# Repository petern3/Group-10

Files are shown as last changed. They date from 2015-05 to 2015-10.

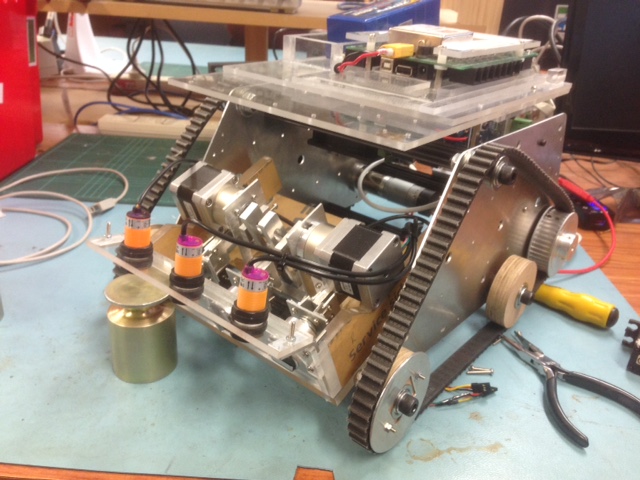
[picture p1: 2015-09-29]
Reports/Photos/IMG_0562.JPG

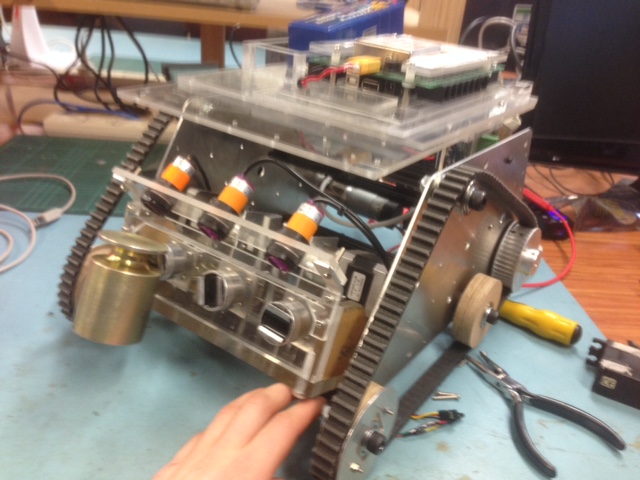
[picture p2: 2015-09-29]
Reports/Photos/IMG_0563.JPG

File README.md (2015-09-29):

# Group-10
Code and reports for the 2015 contest

Authors: Jack, Peter, Ryan

This is a full year assignment which includes:
- Automating a robot to move around a course and retrieve weights
- Writing three progress reports

Useful links
http://www.societyofrobots.com/sensors_sharpirrange.shtml

*Todo*
Mechanical:
- [ ] Track support bring dampers
- [ ] Tilt Mechanism wire test
- [ ] Front brace
- [ ] Reliable weight removal (may come with tilt) stepper driver
- [ ] General tidying up

Electrical:
- [ ] Circuits - ordering parts, PCB
- [ ] Mount IMU etc
- [ ] Limit switches
- [ ] Mount custom circuits
- [ ] Mount other sensors
- [ ] Tidy cables

Software:
- [ ] Redo secondary tactic - wall avoiding, weight detecting, etc with as few 'if' statements as possible
- [ ] Extensive testing and calibrate
- [ ] State estimate
- [ ] State correct
- [ ] Place landmarks (first place that needs map)
- [ ] D*
- [ ] Audio to play off SD

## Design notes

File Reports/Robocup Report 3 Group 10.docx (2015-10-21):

University of Canterbury

# Robocup Progress Report 3

Group 10

Jack Hendrikz
Peter Nicholls
Ryan Taylor

20 October 2015

# 0.0 Executive Summary

This evaluation report (ER) assesses the performance of Group 10s robot in the second annual package-collection Robocup competition. This competition is a challenge where an autonomous robot has 5 minutes to navigate and retrieve as many packages as possible within an unknown arena layout. Group 10 came fourth in a series of knock out rounds. The group competed in a total of four rounds, two of which were won, the other two of which were lost. During these rounds, the robot collected a total 5.25kg worth of food packages, equivalent to just over 1.3kg per round.

The method of package collection was to use three permanent magnets, and used a form of slider-crank to remove the packages from the magnets. Four infrared sensors and three ultrasonic sensors were used to navigate and search the arena. Once a package was seen, it took 0.5 seconds to collect it. The unique track layout could provide a top speed of approximately 0.65ms^(-1) . When a package was collected, an array of digital IR sensors positioned above the magnets confirmed the collection.

This report evaluates the robot against the initial design requirements discussed in the conceptual and detailed design reports (CDR and DDR), followed by a comparison with the four robots challenged. The aspects of the robot that performed well were the permanent magnet collection method and the ground clearance. The two main ways the robot failed was that it could not drop off packages reliably, and the watchdog timer had not been tested in all cases.

The performance of other robots during the competition was variable, with both successes and failures. Group 3 had a robust mechanical magnetic pickup mechanism along with a simple storage and drop off system. Group 12 used speed to their advantage, along with a passive pickup mechanism. Group 6 in contrast had a terrible locomotion system, causing it to become lodged on uneven terrain at several points during the competition.

For the robot to have progressed further in the competition, a better watchdog timer and more reliable package detection should be implemented. This timer, used in tandem with the IMU’s accelerometer, would trigger if the robot had not accelerated for 10 seconds. This would only occur when the robot became stuck against arena obstacles. Package detection had a maximum range of 300mm and could be improved with the use of cameras and infrared diodes.

# 1.0 Introduction

This the final report and assessment for the 2015 Robocup. The Robocup competition is a challenge where an autonomous robot must be designed to search and retrieve packages in an arena. The arena has a series of obstacles unknown to the team, and included walls, poles and uneven ground. The packages are placed in specific but unknown points within the arena, with varying collection difficulty. The packages were also of unknown mass, more mass being worth more points. Two robots competed to get the most mass from the packages.

Each round lasted 5 minutes, and if the winner could not be determined by the total mass collected, then the robot furthest from base would be declared the winner. The competition was structured as a double-elimination tournament such that the winner of each round would continue to the next round, and also allowed for one loss in the competition. The limit of three packages on board meant returning to base was essential to getting more than three packages.

For this to be accomplished, there are many crucial sub-systems that are required to work in unison. These can be split into two main categories:

- Locomotion - how the robot will move, avoid walls and return to base
- Package Manipulation - how the robot will detect, collect and release packages

Both of these require detailed software, electronic interfaces, sensors and mechanical interfaces with the environment. There are also several non-critical subsystems which will also be discussed in lesser details. Such subsystems include the three constructed PCBs.

This report will analyse several aspects of the finished robot, starting with a how it compares with our previous designs in the CDR and DDR, and secondly it's performance in the arena. The performance of our robot against that of four other competitors will also be analysed. Final suggestions for the future evolution of the robot will be put forward as if it was to compete again.

# 2.0 Design Description

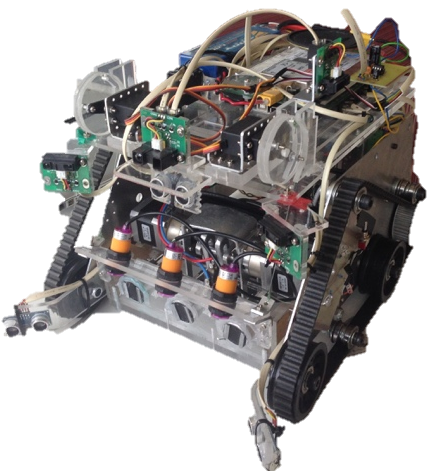
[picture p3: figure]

Figure 1: The final design used in the competition

The final robot design is shown in Figure 1. Three permanent magnets were used to collect and store packages, which could then be raised and lowered using two servos. One ultrasonic and four infrared (IR) sensors were used for navigation, two ultrasonic sensors were used for package detection, and three digital IR sensors were used to detect when a package was on board. 3D printed wheels provided the robot with good ground clearance and greater mobility.

The software we used had effective wall and object avoidance, but had inefficient package detection. Because the ultrasonic sensors used for package detection were noisy, a compromise between response time and accuracy had to be made. Unfortunately we were not able to reliably detect packages which lead to time being wasted by driving past them. Figure 2 shows the overall flow of software used in the competition. The software set a target in Cartesian coordinates to drive towards, which took into account the walls, packages and bases. Using Cartesian coordinates made it easier when linking the sensor information input to driving output.

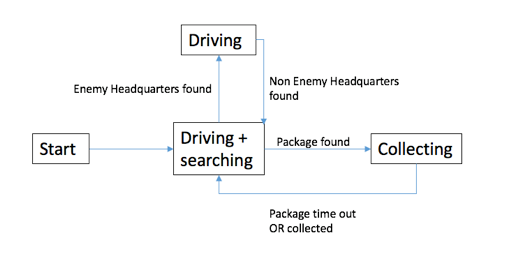
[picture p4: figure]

Figure 2: The final flow of software

## 2.1 Locomotion

### 2.11 Mechanical Layout

The bumps were 17mm high and 3D printed wheels were used to raise the minimum height of the robot to 25mm . Having a shortened wheel base improved the turning speed and mobility of the robot. Although this model did not give a speed advantage, the robot was fast enough that the drive wheels did not require modification. Figure 3 shows the robot track design with the centre of gravity. The track layout was left as described in the CDR and DDR.

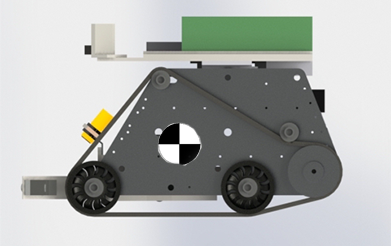
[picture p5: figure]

Figure 3: Track configuration and centre of gravity of the robot

### 2.12 Sensor Layout

One ultrasonic and four IR sensors were used to navigate the arena and avoid obstacles. Two medium IR sensors were mounted on the front of the robot and set at an angle of 27 degrees from the centre-line of the robot. This ensured that they would intersect with the ultrasonic sensor beams which enabled them to be compared. This comparison helped the robot distinguish between obstacles and packages.

The long range IR sensor was mounted in the middle front of the robot and helped with terrain navigation. It was predominantly used to detect corners and allow the robot to move through gaps. It could also be used for pole detection if the robot was approaching the pole.

The centrally mounted ultrasonic sensor was added to compliment the long range IR as it is more effective at detecting poles. This helped ensure that the robot would not become stuck on the poles around the arena. An extra short range IR was mounted on the top of the robot facing left. This aided wall avoidance and helped determine whether it was approaching a corner or not.

### 2.13 Software Algorithms

The software had a series of cases for different sensor readings, each of which would place the target in a different position. This was done approximately every 300ms . Each case compared the sensor values to determine the layout of its surrounding environment, and made suitable navigational decisions. This made it easy to debug each case the robot encountered. There were a total of 16 different cases.

A watchdog timer was also coded to prevent the robot from becoming stuck on obstacles around the arena. To implement a watchdog timer, the location of the target was monitored. If the target had not moved for six seconds, then the robot reversed and then rotated. This method worked well when the robot was stuck in a corner, bump or pole, but caused issues in the presence of another robot, and is discussed later.

This algorithm implemented the secondary tactic, as opposed to the primary tactic due to time constraints. This tactic was described in the DDR but would only be utilised if the primary tactic failed.

## 2.2 Package Manipulation

### 2.21 Pickup Mechanism

The pickup mechanism used three permanent magnets to retain the packages. When a package was detected the robot would lower the magnets ready for collection and once the package was on board it would subsequently raise the magnets. A system was in place to retract the magnets, allowing them to be detached when the mechanism was retracted. In doing so, the magnetic force would be smaller than gravitational force on the packages, thus dropping the packages. Two geared stepper motors (FIT0349) were used to operate the system which converted rotational motion to linear motion. Figure 4 shows the pickup mechanism design with the magnets on the front and digital IR on the front. Figure 5 shows a section view of the mechanism. As the geared stepper rotates the eccentric shaft is spun around, which makes the link rotate back and forward. The magnets are connected through the rod to the link, providing linear motion. Feedback was achieved as to when the magnets were extended by a limit switch, and when a package was being stored by the digital IR sensors. The only changes to this system from the DDR was the addition of a limit switch and reinforcing brackets.

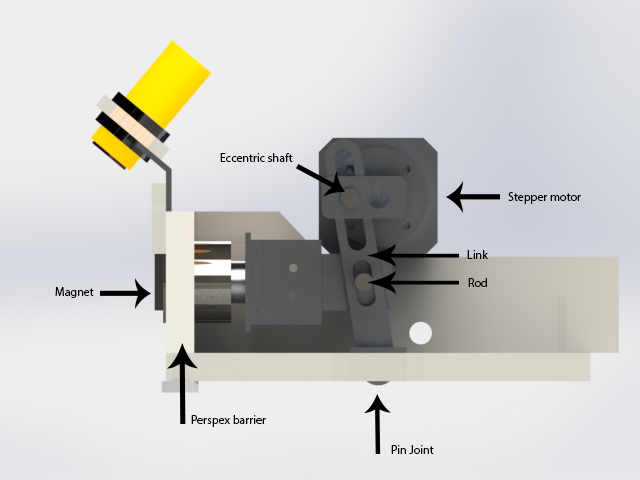
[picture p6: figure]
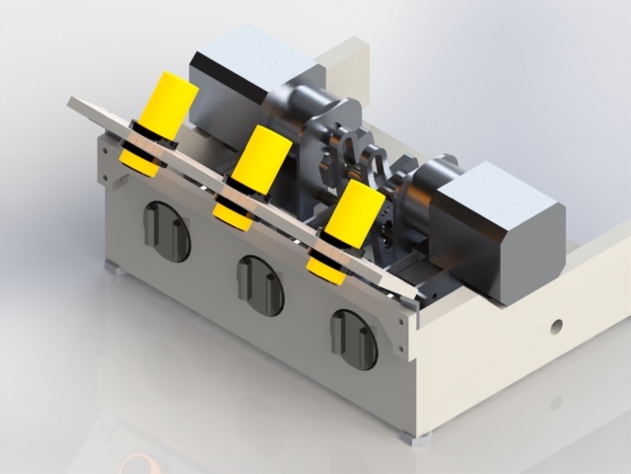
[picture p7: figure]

Figure 4: The overall pickup mechanism

Figure 5: Components within the pickup mechanism

### 2.22 Sensor Layout

Ultrasonic sensors were used to find packages, they were mounted 40mm above the floor in front of the robot. When choosing the angle, if the angle was larger, the robot had a reduced range but had a wider field-of-view. They were placed at an angle of 50 degrees so the viewing angle was a total of 130 degrees. While it could not see packages in the 70 degrees in front of it, these package would fall within view of the ultrasonic sensors at some point. This was as outlined in the DDR.

### 2.23 Software Algorithms

When one of the ultrasonic sensors registered a distance, it would read the IR and ultrasonic sensors on top of the robot and determine whether or not the point given was a wall, pole or package. If it was a package, then the distance was calculated from the difference between ultrasonic sensors and IR sensor, and then the relative Cartesian coordinate would be computed.

When a package was detected, the robot placed the target on top of the reading. To reduce the effect of 'false positives' given by the ultrasonic sensors, three checks were done. Firstly, the robot would only decide that a package was indeed a package after detecting it three consecutive times. Secondly, the amount of time spent chasing the package was directly proportional to the number of times detected. This allowed time to pick up the package once in the robot's inner blind spot. Thirdly, when aligning with a package, the robot would move slower. This was good as it has reduced probability of driving into walls, but it also made it much slower when nearing a package (as the speed was proportional to the distance from the target).

Because there were three digital IR sensors which could determine which magnets had collected packages, the robot could aligned such that the packages would collect on the empty magnets. When all three digital IR sensors were active, the robot would not attempt to collect packages. The robot would also not collect packages when it either base. This was how the DDR described the package detection.

## 2.3 Non-crucial Subsystems

### 2.31 Audio Amplifier

Since the Arduino is not able to supply much current, attaching a speaker straight to the pins could not provide the volume wanted. The amplifier board was so successful that while it was not receiving a signal, it would amplify the electrical noise generated by the fan. To prevent this, a transistor was used to enable or disable the speaker. This meant it would be enabled only when it needed to be used.

### 2.32 Switch bank

The bank of eight switches was a useful addition to the robot which ought to have been implemented earlier. Although it wasn't really used in the actual competition, it was very useful when testing. Each of the switches were bound to a different statement in code which enabled different behaviours such as whether or not to release packages and disabling the motors. Each of these were useful when testing.

### 2.33 Light Array

This was initially intended to contain a bank of IR LEDs as well as mount the IR camera, there was not sufficient time to implement the camera. As such, the IR LEDs were not required, so standard LEDs were used for nothing more than to confuse other robot's cameras.

# 3.0 Design Evaluation of Robot

## 3.1 General

#### R1.1 The robot will be fully autonomous ✔

#### R1.2 The robot will be controlled by the Arduino Mega ADK supplied ✔

#### R1.3 The robot shall be able to move, identify and collect packages ✔

#### R1.4 The robot shall operate until all 11 packages are claimed or the time limit is reached ✔

The robot was fully autonomous throughout the competition through the use of the supplied Arduino Mega ADK as specified in R1.1 and R1.2. The robot had the ability to move, identify, and collect packages within the arena with the use of ultrasonic sensors as per R1.3. During the tournament, the robot collected seven packages, weighing a total of 5.25kg . Although the robot collected this many packages, there were another approximately 20 packages that were either not detected (and should have been) or unable to be collected at all. This gave the robot a successful collection rate of 35%.

The robot fulfilled R1.4 as it operated for the full five minutes that the match lasted. There were not issues with the robot running out of power during operation, but the robot was immobilised during the third round. It could be noted that there was no counter implemented to instruct the robot to cease package detection after all 11 packages had been claimed.

## 3.2 Identification

#### R2.1 The robot shall be able to identify food packages ✔

#### R2.2 The robot shall be able to identify obstacles it cannot move over ✔

#### R2.3 The robot shall be able to distinguish home HQ and the opposition HQ ✔

#### R2.4 The robot should rely on a range of navigational sensors ✔

The robot could identify packages as per R2.1, however it did have reliability issues. It detected approximately 60% of the packages within the sensors’ range, but there were also several false positives detected. The arena walls had a curved skirting which on occasion would be read as a package. Poles were also another obstacle that would flag a false positive due to the offset of the ultrasonic and IR sensors. While they were placed to reduce false positives, there was a small region in front of the robot that is detected by the ultrasonic sensor but not the medium IR sensors, and was hence interpreted as a package. This meant that the robot moved towards what the false ‘package’. Once the robot was close enough, the sensors could not read accurately. This is when the watchdog timer kicked in and caused the robot to reverse and turn. The false positives could have been reduced through the additional use of an alternative package detection system.

The robot performed well when it came to identifying its surrounding environment. The use of four different types of navigational sensors satisfied R2.2 and R2.4. A total of five sensors were used for navigation along with two sensors for package detection. This sensor array meant the robot reduced collisions with the arena to approximately four per minute. The only problem encountered during the competition when navigating was that the robot often steered towards poles (as discussed previously), which raised this collision rate to over six per minute.

Once calibrated, the robot could accurately distinguish between home HQ and opposition HQ. This was achieved via the Adafruit TCS3472 colour sensor mounted on the underside of the robot. The robot never attempted to collect a package in either base, and so R2.3 was satisfied. Overall the robot's environment detection performed well at a basic level during the competition, but could have functioned more robustly with more comprehensive calibration and testing.

## 3.3 Movement

#### R3.1 The robot shall be able to move over obstacles at least 25mm in height ✔

#### R3.2 The robot shall be able to fit through gaps of at least 500mm in width ✔

#### R3.3 The robot shall be able to manoeuvre around obstacles it cannot move over ✔

#### R3.4 The robot shall not leave the designated arena during the competition ✔

#### R3.5 The robot should not get stuck in any algorithmic loops for longer than 1 minute ✘

The design of the locomotion allowed the robot to operate well within the arena during the competition. The 3D printed wheel and track design allowed the robot to drive over obstacles at a speed of about 0.65ms^(-1) as per the requirements of R3.1. The design was kept compact, allowing the robot to move through arena obstacle gaps of at least 500mm , specified in R3.2. Once obstacles too large to move over were detected, the robot could navigate efficiently around them, thus fulfilling R3.3. There was no physical way that the robot could leave the arena during operation, meeting requirement R3.4.

The robot did suffer from a few design issues, one of which was that the tracks detached occasionally, once during the competition. This only happened on uneven terrain, as the belts lost tension and subsequently slipped off the wheels. This could have been avoided through providing more belt tension and installing brackets to prevent the belt from slipping off the wheels.

During testing it was noticed that the front of the aluminium chassis would flex outwards by 5mm on both sides. This flexing was put down to the belt tension and lack of bracing on the front of the robot. Bracing was difficult to achieve as it would have obstructed the pickup mechanism. Side bracing could have solved this issue, but there was insufficient time to test this solution.

For R3.5, steps were taken to prevent the robot from getting stuck in algorithmic logic loops for longer than one minute, however, not all issues were remedied before the competition day. A watchdog timer was implemented to prevent the robot from becoming stuck on terrain in the arena. This worked when stuck against terrain, but had not been tested with another robot. As the opposition robot moved, the robot's target would change and therefore reset the timer. In addition to checking the change in target, the accelerometer could have assisted in detecting when the robot had stopped.

## 3.4 Collection

#### R4.1 The robot shall be able to pick up a package so that it is under the robot’s control ✔

#### R4.2 The robot shall have a way of carrying, at most, three packages without hindrance ✔

#### R4.3 The robot shall not collect any packages within the opposition’s HQ ✔

#### R4.4 The robot should be able to release any packages it has on-board to HQ ✘

#### R4.5 The robot should be able to pick up packages in any orientation and any part of the map ✘

The collection mechanism of the robot performed well in the arena, and was the sole reason that the robot succeeded on the day. The versatility of the permanent magnets allowed three packages to be picked up under the robot's control, thus fulfilling R4.1 and R4.2. Two HX12K servo motors were used to lift the pickup mechanism for two reasons: so that the packages did not catch on uneven ground, and to prevent collection of opposition packages within their HQ. This meant that the robot also met criteria R4.3 during the competition.

The robot was programmed and designed so that packages could be dropped off in its HQ when the corresponding colour was detected. The magnet strength was underestimated during the calculation phase of the robot, preventing reliable package removal. This still would have been sufficient to remove some packages, but the mechanism would try to retract within the arena during last minute testing. This was either due to final changes in code or the lighting conditions. As such, the magnet retraction was disabled for the competition, which wasn't a big issue as the robot never collected three packages at one time. Even though functionality was there to remove the packages, it was not implemented during the competition and does therefore not meet R4.4. The packages also had a tendency to rotate when attached to the robot, making it difficult for other subsequent packages to be retrieved, which is the primary reason why the robot did not collect more packages in two of the rounds.

The robot could successfully pick up packages in any orientation in the arena but could not always collect packages placed close to obstacles as required by R4.5. It could not pick up packages near walls due to the wall avoiding aspects of the program. This could be helped by improving the package detection system, allowing the robot to get nearer to walls. It also could not collect packages on the opposite side of uneven ground as the pickup mechanism obstructed movement when trying to collect packages. This would most easily be fixed with a skid to mechanically lift the mechanism on uneven ground.

This robot had one of the most efficient pickup mechanisms, being able to collect a package in 0.5 seconds, rivalled only by Group 12’s mechanism. The average mass of packages collected per round was 0.7kg , which was nearly half that of our robot, which collected an average of 1.3kg .

## 3.5 Construction

#### R5.1 The cost of additional items shall not exceed $50 (except for R5.2) ✔

#### R5.2 Each member shall design their own PCB for use on the robot, not exceeding $5 ✔

#### R5.3 The robot should be built with less than 200g of 3D printer plastic. ✔

#### R5.4 The robot shall be easy to maintain and disassemble ✔

The construction of the robot met all the requirements. The additional components came to a total of $32.50, thus remaining under the limit of $50 as required in R5.1. A bill of materials can be seen in Appendix 1. The circuit boards designed were an amplifier circuit, an LED bank, and a dip switch circuit. Each circuit was built for less than five dollars, which satisfied R5.2. The 3D printed wheels used had a combined mass of 180g , thus meeting R5.3.

Once the mechanism allowing the packages to be lifted or lowered was added, it was slightly harder to disassemble the robot. This was not a major problem and did not significantly hinder the ability to maintain or disassemble the robot. Therefore, the robot met specification R5.4.

## 3.6 Safety

#### R6.1 The robot shall not cause any deliberate damage to anything or anyone ✔

#### R6.2 The robot shall have an accessible ‘off’ switch ✔

#### R6.3 The robot shall use the battery safety circuit provided ✔

The robot was designed to minimize potential safety risks during operation inside and outside of the arena. Parts that were moving were difficult to access, making it hard to injure people or damage other robots. Machined components were sanded to remove all sharp edges. This ensured that the robot could meet specification R6.1. The power switch was place on the inside of the robot for easy access to meet R6.3 whilst being protected from opposition robots. The off switch ensured that the robot could be powered down at any time. The provided battery circuit was implemented as specified in the competition briefing, therefore the robot met criteria R6.3. Overall the robot design was very safe with minimal potential health and safety risks.

# 4.0 Performance of Other Designs

## 4.1 Competitor 1 (Group 4)

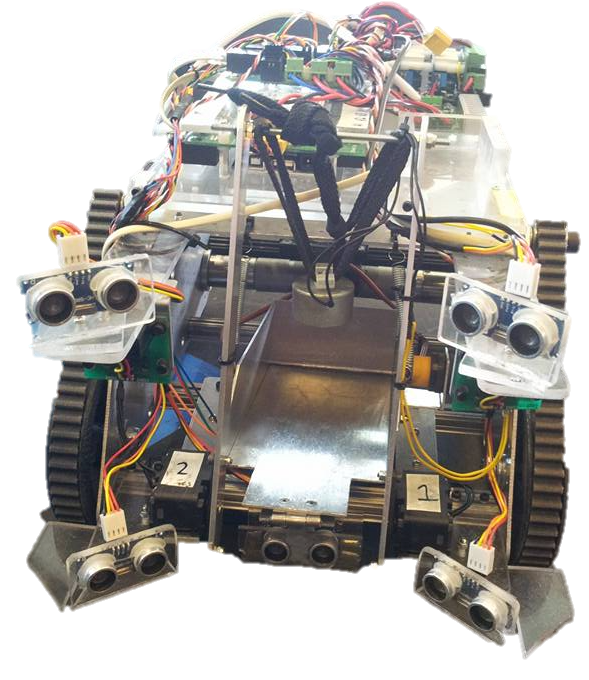
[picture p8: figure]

Group 4 employed the use of an electromagnet setup on a crane system (see Figure 5). The robot would approach the package and line up using ultrasonic sensors. Once in position, the crane was extended and the magnet was switched on, allowing the package to be collected. The robot's speed was approximately 0.5ms^(-1) . Obstacle avoidance was achieved via two front mounted long range IR sensors.

Figure 5: Group 4 robot

Package detection was achieved via five ultrasonic sensors. The upper ultrasonic sensors were compared with the lower ultrasonic sensors, as our robot did. The robot would then line up and centralise using the lower sensors. Once this was done then the central ultrasonic sensor was used to determine distance. Packages could be detected at a distance of approximately 400-500mm , however the field of view was limited. The robot could align and pick up a package in around five seconds. Packages could be picked up in any orientation, however the robot had difficulty detecting fallen packages. As quite a few packages were knocked over during the competition, it was difficult to determine the number of successful collections after package detection.

During the competition this robot could pick up packages well once they were detected. The speed of package retrieval was one of the main issues with this robot, as it was much slower compared to ours. Obstacle avoidance was also an issue as the only two long rang IR's were used. Our robot too could have used electromagnets, which would have simplified the pickup mechanism significantly. In summary this design would have functioned better wither more accurate obstacle and package detection.

## 4.2 Competitor 2 (Group 3)

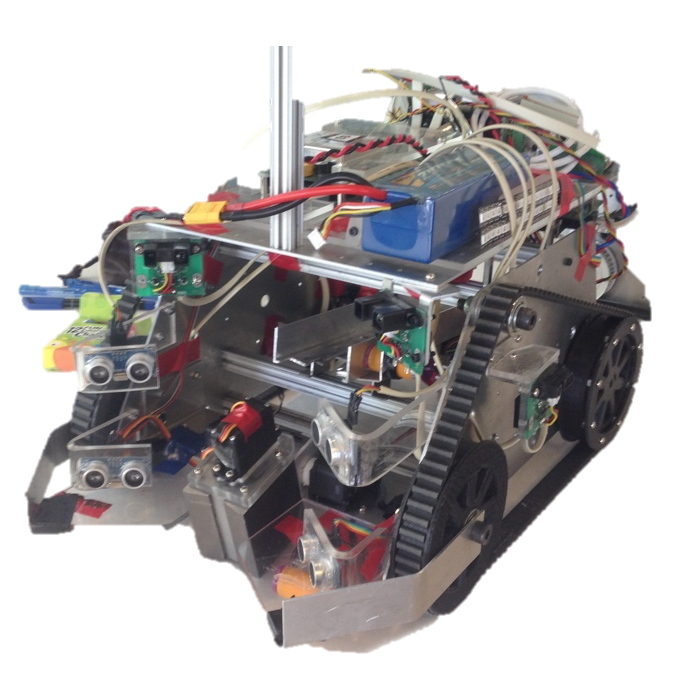
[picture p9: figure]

Group 3 employed the use of a switchable permanent magnet that could be switched on or off depending on the orientation of the stepper motor (Figure 6). The robot would align itself with the package and engage the magnet. Next, a smart servo was used to lift up the package and place it on board the robot. The robot's travelling speed was approximately 0.6ms^(-1) . Obstacle avoidance was achieved via two cross long range IR sensors and side mounted IR sensors.

Similar to other designs, package detection was achieved by ultrasonic sensors. Like Group 4, packages were detected by comparing upper and lower ultrasonic sensors, which gave a field-of-view of 135 degrees, and a maximum detection range of 600mm.

Figure 6: Group 3 robot

This robot did surprisingly well in the competition, placing third overall. The pickup mechanism and holding mechanism worked well, although the packages sometimes had a tendency to fall off the magnet during pickup and become lodged on top of the ultrasonic sensors. This robot seemed a fair bit slower than the other robots during the competition, with a collection time of 5.8 seconds. It also struggled to detect packages in the arena, which was the design’s major shortcoming. In summary, this robot had potential but several drawbacks prevented it from winning the competition.

## 4.3 Competitor 3 (Group 12)

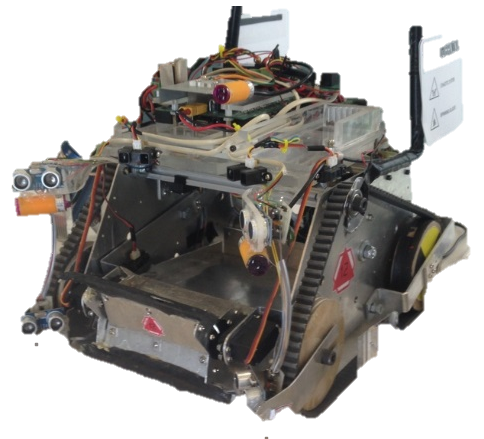
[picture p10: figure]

Group 12 employed the use of a combine harvester sweeping collection mechanism which would grab hold of the packages and sweep them on board the robot (Figure 7). This mechanism worked well as it could pick up packages even if they were not detected by the ultrasonic sensors. Because of this, the travelling speed of this robot was much faster than most robots, being approximately 0.8ms^(-1) . Obstacle detection was achieved by long range IR sensors, variable IR sensors and high velocities.

Much the same as Groups 3 and 4, package detection was achieved by ultrasonic signal comparison. Packages could be detected between 40 and 400mm . The robot had a field-of-view of approximately 50 degrees either side of the centre line. Detection of package wasn't very accurate, but this group did end up collecting the most package overall and hence the greatest mass. Once packages were detected, the robot simply drove at the package. If the package became jammed, then it could be ejected by reversing the pickup mechanism. Pickup time was between 0.5 and 2 seconds. Once three packages were on board then the robot used the IMU to return to base via the built in magnetometer.

Figure 7: Group 12 robot

This design worked well during the competition as it could pick up package in any orientation and return to HQ once three packages were collected. This design could have been significantly improved with a more accurate package detection mechanism. Our robot could have benefited significantly by using the IMU to return to HQ once three packages were detected, the only issue could have been the permanent magnets interfering with the IMU magnetometer. Overall this robot deserved a higher placing than it achieved in the competition.

## 4.4 Competitor 4 (Group 6)

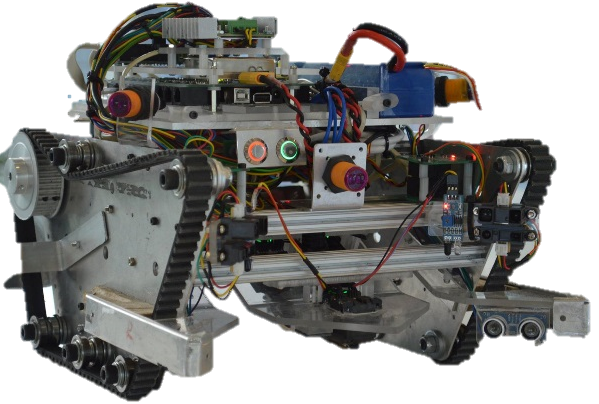
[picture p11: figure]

Group 6 employed the use of a slotted pick up mechanism which swept the packages on board and held them via their groves (Figure 8). The robot would align itself with the package, then the smart servo controlled bar would sweep the package up the slot and store the package at the rear of the robot. This was a fairly slow robot, so a travel speed of 0.4ms^(-1) would be a good approximate. Obstacle detection was achieved through an array of IR sensors.

Figure 8: Group 6 robot

Package detection used ultrasonic sensors similar to the other groups evaluated in this report. The difference being that the ultrasonic signal was compared with short and long range IR sensors mounted above. This robot was supposed to have been able to detect packages from 0 to 700mm , but this would seem to be a very optimistic estimate. Once a package was detected, the robot took approximately five seconds to drive to the package and collect it. This design was limited by the fact that it could only retrieve packages that were upright and not obstructed by obstacles.

Similarities to our robot was seen in the comparison of signals between the infrared and ultrasonic sensors. During the competition, this robot struggled to manoeuvre over terrain. However, its package detection and pick up mechanism seemed to work well when packages were lined up. Overall this robot operated adequately and achieved second place in the competition, but improvements to locomotion would have further helped this robot.

## 4.5 Design Improvements

During the competition, the robot lost a total of two times. These were due to a number of issues that could be improved on in order to produce a winning robot. The first round lost was to Group 3 when our robot became locked with the opposing robot. The round came to an end after five minutes, and they won as they were further from their base – both robots carried the same mass. It is difficult to prevent robots locking together, and it is even more difficult to program them to separate once it has occurred (which our robot did). The best way to avoid this would be to have better sensor placement in order to avoid collision with the opposition's robot. Overall better package detection and sensor placement would have avoided this loss.

More reliable package detection would improve many aspects of this robot. Currently, the use of ultrasonic sensors to detect packages has issues with false detections caused by arena obstacles. These false detections caused the robot to waste time looking for packages and caused the robot to become stuck at several points during the competition. This could be achieved via several different methods that are within the boundaries of the competition. Computer vision could be used to navigate as well as look for packages, as the brass colour is quite distinctive. Another option would be the use of an IR diode coupled with an IR camera. The package in the arena would reflect the IR wavelengths and appear as bright spots within the arena. These bright spots could be picked up by the IR camera, allowing the robot to hone in on the package. Both these options should definitely be investigate further to produce a better performing robot.

The second loss occurred when facing Group 6. The opposition robot became stuck in front of our robot on top of uneven terrain. Our robot, without a reliable watchdog timer, continued to drive into the opposition robot thinking that it was collecting a package. This could be avoided through the use of a watchdog timer that used the accelerometer. If the robot hadn't moved for 10 seconds then it would trigger the timer to reverse, turn, and drive away. If our robot backed up from getting stuck, it would have been likely to collect more packages.

# 5.0 Conclusion

In conclusion, the robot designed by Group 10 for the Robocup competition was a well-rounded robot that had good potential. It had an effective and unique track layout, allowing the robot to move fairly quickly and efficiently over all terrain, and the robot also possessed one of the two most efficient methods of package collection.

Although this robot had these effective systems, there were several weaknesses this robot had which caused the robot to fail twice – and lose the tournament. There are two primary changes that have been identified as most important, one of which would require much re-working, and the other which would only require several hours to implement. The package detection method of using a difference in sensor values was not sufficient, but should be complimented with a larger variety of sensors, and the watchdog timer would have been made more effective by using accelerometer values as well.

Throughout the course of designing and constructing this robot, many lessons have been learnt, and many tasks would be done differently next time. Although our robot did not win the Robocup, it has been an all-round positive experience for the whole team.

# Contribution statements

Ryan Taylor

- Report writing and formatting
- CAD modelling/drawing
- Pickup mechanism design, calculations, Matlab coding and build/machine
- Material/Parts sourcing
- Circuit 3 (LED Array) design and build
- Software logic and testing

Jack Hendrikz

- Report writing and formatting
- Design and building of electrical module (sensor circuit layout and wiring)
- Quick release mechanism design
- Circuit 1 (Audio Amplifier) design and build
- General testing, coding and debugging

Peter Nicholls

- Report proof-reading and formatting
- Electrical to Software interfaces
- Navigation algorithm research
- Software design and implementation
- Circuit 2 (Switch bank) design and build

# Appendix 1 – Bill of Materials

## Bill Of Materials (Provided)

Item | Quantity | Total Cost (NZ dollar)
Aluminium plate | 2 | 32.00
Aluminium extrusion | 4 | Not priced
Sensor Circuits | 4 | Not priced
Arduino Mega ADK | 1 | 60.00
Lithium Battery | 1 | Not priced
Ultrasonic Sensor | 2 | 2.00
Medium Infrared Sensor | 2 | 38.00
Long Infrared Sensors | 1 | 17.00
Cables | NA | Not priced
3D Printed Wheel | 4 | Not priced
Smart Servo | 1 | 50.00
DC motor | 2 | 106.00
Drive Wheel | 2 | Not priced
Bearing (29mm) | 16 | Not priced
M3 Cap Screws | NA | Not priced
M8 Cap Screws | 10 | Not priced
Aluminium 15mm 40x100 | 1 | 5
Aluminium 5mm 120x100 | 1 | 10
Aluminium 2mm 300x200 | 1 | 5
Steel rod 1/4 inch 200mm | 1 | 1
Steel rod 10mm 100mm | 1 | 0.5
Spring 20mm compressive | 1 | 0.1
Perspex 10mm 200x350 | 1 | Not priced
Perspex 4mm 200x150 | 1 | Not priced
M3 | 40 | 4
M5 | 4 | 0.75
Geared Stepper | 2 | 30
Digital IR | 3 | 15

## Bill of Materials (Additional)

Item | Quantity | Total Cost (NZ dollar)
Ultrasonic sensor | 1 | $2.50
Permanent Magnets | 3 | 30.00
Total Cost | | $32.50

## Bill Of Materials (Circuit 1)

Item | Quantity | Cost (NZ dollar)
1000 uF/ 25V electro cap | 1 | 0.22
10 uF/ 25V electro cap | 1 | 0.10
0.22 uF/ 25V electro cap | 1 | 0.10
100 n cap | 1 | 0.05
47 n cap | 1 | 0.40
IC LM386 | 1 | 0.08
10k variable resistor | 1 | 0.33
10 Ω resistor | 1 | 0.02
1 W speaker | 1 | 1.50
Total Cost | | $2.80

## Bill Of Materials (Circuit 2)

Item | Quantity | Cost (NZ dollar)
SW DIP-8 | 1 | 2.51
RJ45 8P8C jack | 2 | 0.50
Resistor 10K | 8 | 0.02
Total Cost | | $3.67

## Bill Of Materials (Circuit 3)

Item | Quantity | Cost (NZ dollar)
IR LED | 6 | 0.20
220 Ω resistor | 6 | 0.02
Header pin | 2 | 0.10
Switch | 1 | 3.00
Total Cost | | $4.52

# Appendix 2 – Tournament Placings

Group | Place | Total mass (kg) | Rounds contested
1 | 10= | 0.75 | 2
2 | 10= | 0 | 2
3 | 3 | 3.75 | 5
4 | 7= | 3.25 | 4
5 | 10= | 0 | 2
6 | 2 | 6.5 | 8
7 | 7= | 3.25 | 4
8 | 10= | 0.75 | 2
9 | 5= | 1.5 | 4
10 | 4 | 5.25 | 4
11 | 1 | 6.5 | 6
12 | 5= | 6.75 | 4
13 | 9 | 1 | 3

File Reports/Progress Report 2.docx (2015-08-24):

University of Canterbury

# Robocup Progress Report 2

Group 10

Jack Hendrikz
Peter Nicholls
Ryan Taylor

24 August 2015

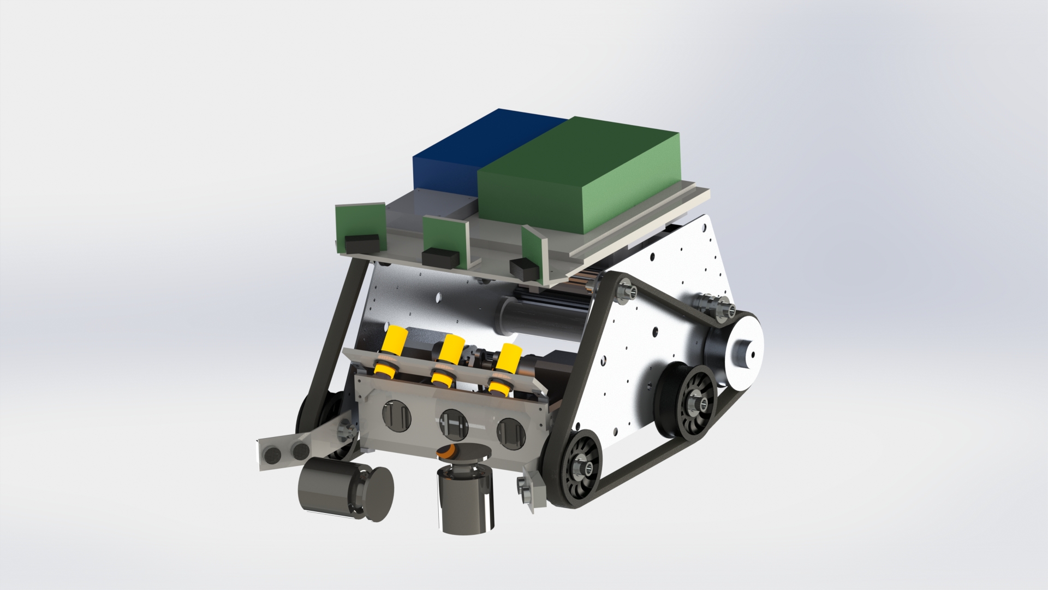
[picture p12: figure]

# 0.0 Executive Summary

This report discusses the design of Group 10’s robot that will be entered in the Robocup challenge in October this year. The robot has already performed well in the initial functionality assessment, achieving a perfect score.

Three modules are presented with a detailed overview in this report. The mechanical system module includes the robot chassis, locomotion method and package collection. Next the electrical system module includes an evaluation of sensors used, their position on the robot, and the circuits created for further functionality. Finally there is the software module which includes all the programming required to allow the robot to function autonomously.

An evaluation of each module is conducted to contrast the current functionality against the robot’s requirements outlined in the initial report. The report also contains a future development section that discusses the changes that should be made to the robot before the final competition.

The robot has currently completed 17 of the 25 requirements and performed well in the functionality assessment. It can detect objects such as walls but has some issues with pole detection. It can identify, move to and collect packages around the arena but there is much to be improved. The code allows for wall avoidance, but pathfinding is yet to be implemented. Overall the robot is well on its way to performing as specified on the test date and will be significantly improved over the following months.

# 1.0 Introduction

In this year’s Robocup Zombie apocalypse, teams have designed robots that search autonomously for food packages. The robot will compete in the arena against another robot for these packages. The battle will take place in an unknown environment which includes immovable obstacles, walls, and a series of rough sections of ground all unknown to the robot. The robot will need to return food packages to the team’s headquarters. These food packages are represented by cylindrical weights made from steel weighing between 0.25 and 1 kilogram, and will be placed in both easy and hard to reach places.

This report takes our chosen design from Conceptual Design Report (CDR), and explains the technical details on how the robot is built and how it will complete the tasks. As a mechatronic system, the details are split into mechanical, electronic and software design, each of which are crucial for an effective, autonomous robot.

# 2.0 Mechanical Design

## 2.1 Chassis

The design will use the chassis supplied as it will take too long to design and construct a better one. The one supplied gives good mounting holes for the wheels in various positions. As discussed in the previous report, parts have been modified so the chassis is oriented up-side down.

## 2.2 Locomotion

Locomotion is one of many essential tasks for the robot to succeed. When designing the wheels several aspects must be taken into account: maintaining the tracks on the wheels, getting enough traction on the track from the motor, having enough ground clearance and where the tracks will contact the ground. The drive motors will be two 12V low noise 28PA51G DC motor, these will remain in their initial position on the chassis wall.

Opting for 3D printed wheels allowed the ability to have control over all these parameters. This also meant they could be designed in Solidworks and modelled appropriately to meet the parameters. Having the correct lip on the edge of the wheel is essential or else the track may come loose, this was modelled and a suitable lip designed. To get traction from the drive wheel to the track relied on getting the greatest amount of surface area with sufficient tension. A high amount to traction was achieved by having nearly 180 degrees of contact with the wheel. Since the maximum ground obstacles are 25mm in high, the radiuses of the wheels were made to be 30mm, also allowing for the mounting holes. By keeping the track-ground contact area small will improve manoeuvrability, but would result in decreased stability, and this was taken into account when choosing how much length of track would touch the ground. The kit was designed with a length of about 200mm, or 250mm when inverted as was our chassis. The length chosen was 200mm in order to counteract this disadvantage of the inverted chassis. Solidworks calculated the centre of mass of the robot to be in the centre of the track length which is ideal, seen in Figure 1.

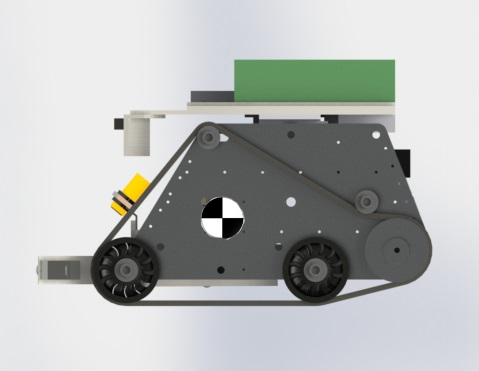
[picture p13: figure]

Figure 1, Shows the side of the robot with the wheel design and the centre of gravity.

## 2.3 Package collection

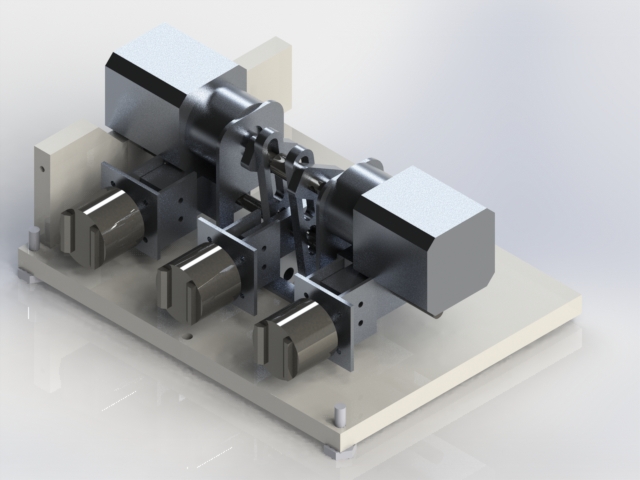
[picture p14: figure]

The mechanical element of the build requires a system to pick up and store three packages. The main principle for our design will be using magnetic force to pick and store packages. Three strong magnets in a row along the front of the robot will be ready if any packages are detected to pick them up. Once three packages are picked up then the robot will drive back to base and drop them off by retracting the three magnets though the perspex barrier. The force of the three magnets requires a greater force to retract them. This greater force has to overcome the 450N (worst case) from the attraction between the magnets and packages. To get this force two geared stepper motors, FIT0349, will be used in junction with a reciprocating mechanism. This mechanism changes rotary motion to linear motion and also gives a step up force simultaneously. Figure 2 shows the overall mechanism and Figure 3 shows more detail of the moving parts.

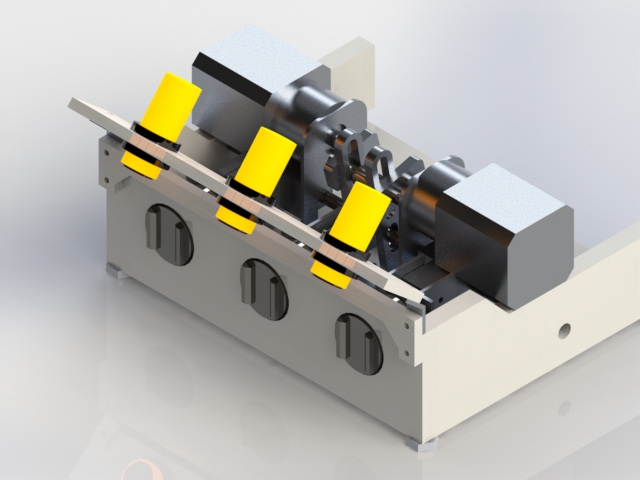
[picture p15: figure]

Figure 3, Shows a stripped away picture of the pickup mechanism.

Figure 2, Shows the overall design for the pickup mechanism.

Linear motion is provided by a simple slider crank idea, shown in Figure 4. Two geared steppers are mounted facing each other on a bracket holding them in line for direct drive. The two geared steppers are needed to provide enough torque. These motors have an eccentric shaft between them, this gives the torque. The eccentric shaft can slide up and down a link, the other end of the link is pinned on the bottom of the mechanism. Down the link a rod, parallel the eccentric shaft, is restricted to horizontal movement. A connection is made between the three magnets and the rod. The magnets are mounted in the front held in by a perspex barrier. When the link sways back and forth it push and pulls the rod thus moving the magnets in and out. All the custom parts have been machined.


Figure 4, Shows a side view of the pickup mechanism with labels showing different parts.

Figure 5 is an exploded view of all the parts for the pickup mechanism.

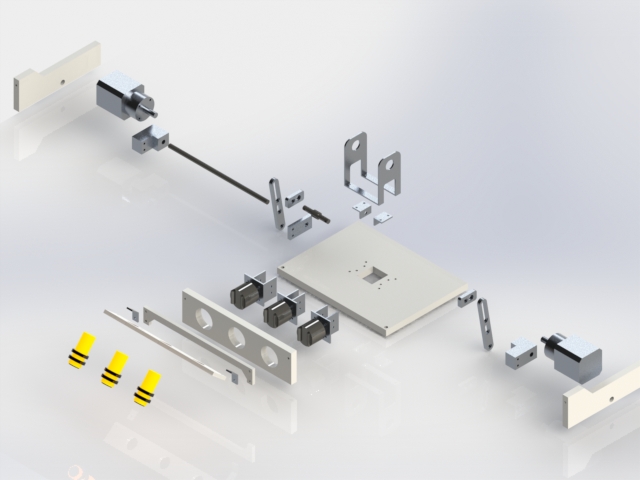
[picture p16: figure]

Figure 5, Shows an exploded view of the pickup mechanism parts.

Ensuring the packages fall off when the mechanism is operated is essential for the robot’s correct operation. The mechanism uses two stepper motors with a torque of 1.78 Nm each. To make sure this happens, Matlab was used to find various lengths that would successfully retract the magnets, seen in Figure 6. The blue line shows the force needed to release the magnets and the red line is the calculated force applied to the magnets. The packages will be dropped off between 80 to 160 degrees. This is a small band of the force curve that the figure shows will be enough force to drop the magnets off. The reason the second peak of the curve is lower than the first is because when the eccentric shaft is on the lower side of the turn, less torque is transferred. See Appendix 1 for the code and hand calculations. This calculation doesn’t take into account mechanical losses or the stall torque of the motors so the force produced will be less than shown. This shouldn’t be a problem given that the maximum force is nearly double that required.

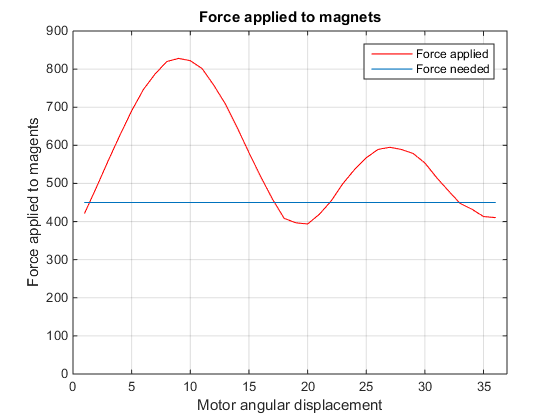
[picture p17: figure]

Figure 6, Shows the force produced by the pickup mechanism applied to the magnets.

The design focusses on overcoming big problems that could put a halt to package collection, which consisted of different orientation packages (fallen over), packages tight corners and fast and simple package collection. If the other team knocks the packages over then the packages can still be recovered due the high attraction force of the magnets, and if the opponent can’t recover fallen over packages then it will be an easy win. Secondly, having the two of the magnets off centre of the robot will allow for corner collection easier. Finally, the actual collection of packages is fast, simple and reliable, as the robot merely needs to run into the package for it to be permanently on board.

Because it can pick up packages this easily, there needs to be some method of not collecting packages in the opponent’s base. To ensure this is the case, the whole pickup mechanism tilts up and down, and also prevents the packages from getting jammed against a ground obstacle. The majority of the time the robot will drive with the mechanism raised, but will only lower to collect a package. Once the robot has driven into the package and confirmation the package is on board will raise the mechanism. Tilting will take about five seconds to complete, so the collection will be a total of just over ten seconds.

Drawings for the mechanical systems can be found in Appendix 7.

# 3.0 Electrical Design

## 3.1 Circuit Boards

In order to drive the sensors and motors with the correct voltage and to receive the desired signals for the sensors, the provided circuit boards must be implemented into the robot design. All the provided power and interface circuits were used except for the servo interface board. The Arduino and battery were placed on the top of the robot, while the rest were mounted on the underside of a Perspex sheet below the Arduino. Figure 7 demonstrates the connections between each of the boards and the components. It can be noted that the ‘Power Safety Circuit’ shown is also a distribution board.

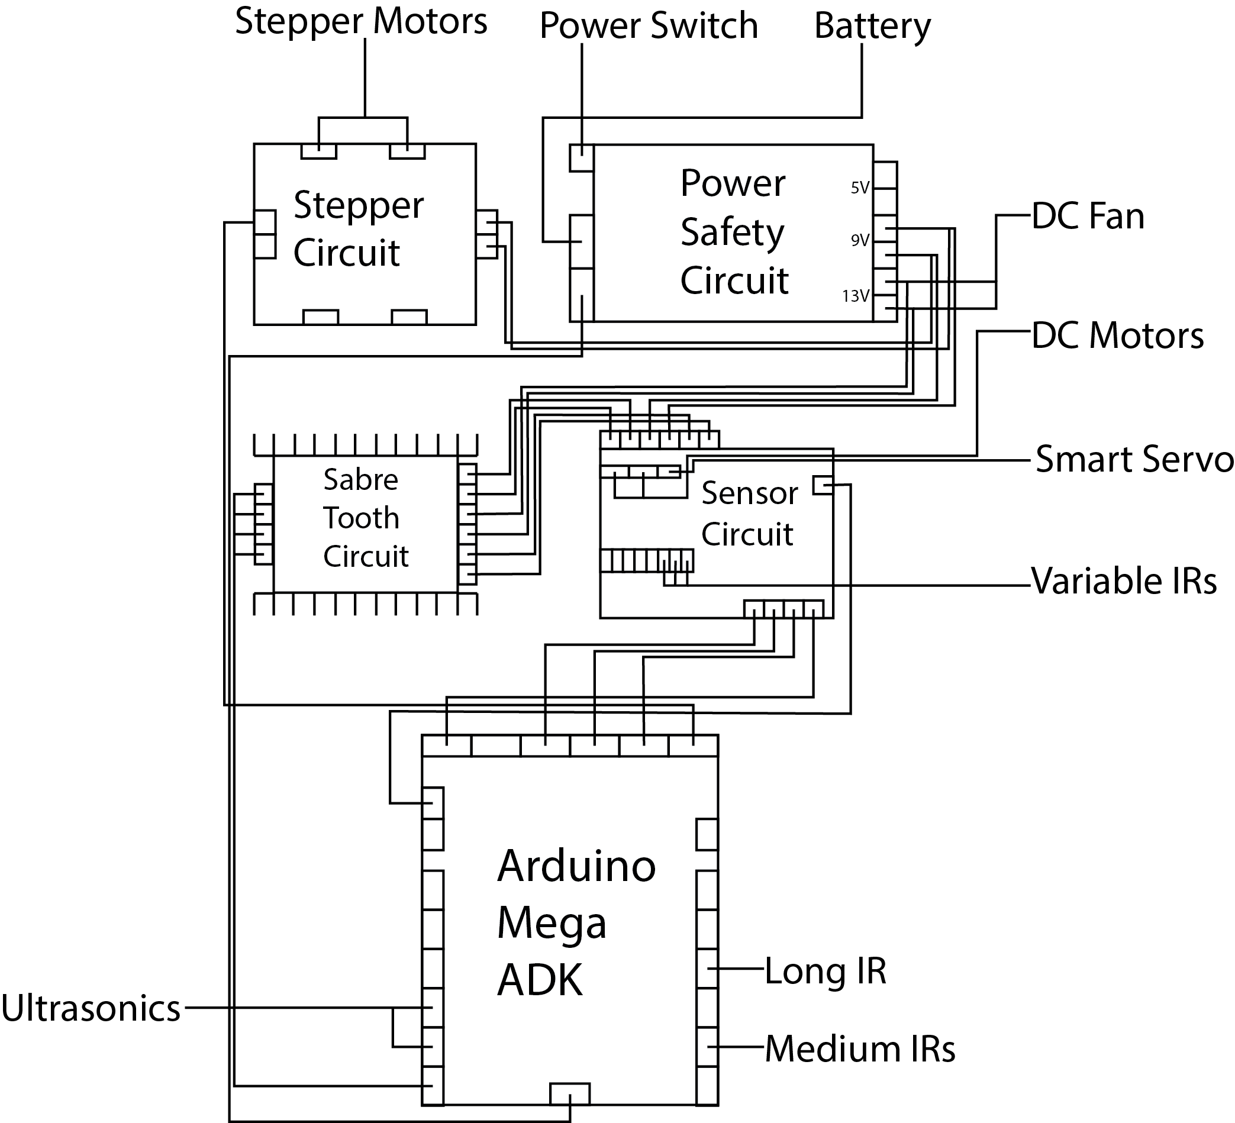
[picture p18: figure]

Figure 7, Shows the overall electrical circuit board connections.

Having the circuits on one piece of Perspex allowed the boards to be arranged in a compact design that could be easily accessible. The boards were arranged in such a way that they could be connected easily to one another as well as the Arduino. The cabling could be neatly run without the risk of interference with the pickup mechanism or the risk of potential damage by being exposed externally on the robot. Most importantly, every individual board could be accessed due to a through a quick release mechanism allowing the mount to swivel. Easy access of the boards is seen in Figure 8.

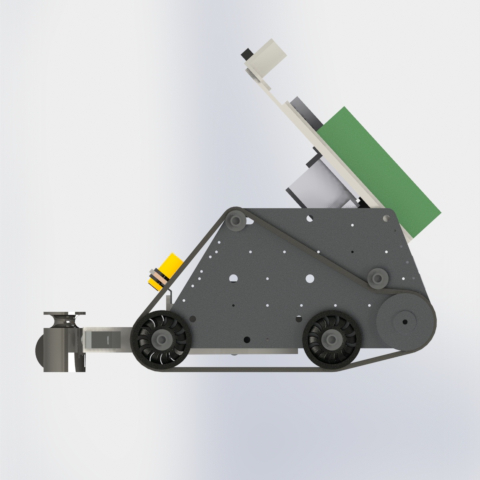
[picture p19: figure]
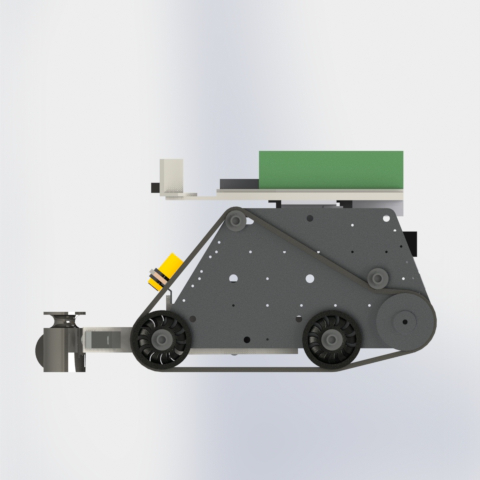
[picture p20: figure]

Figure 8, Shows the quick release mechanism rotating.

As part of the concept specifications, it was required that each group member design a circuit board to aid in the functionality of the robot. These three circuit board designs are presented in the following sections, and the schematics can be located in Appendix 2.

### Circuit 1: Small speaker amplifier

This circuit is used to amplify audio signals sent from the Arduino as they are too weak to drive the speaker directly with significant volume. This circuit will consist of a LM386 IC chip, along with the necessary resistors and capacitors to drive a 1 watt speaker at 8 Ohms. The circuit will have a variable volume control via an adjustable potentiometer.

### Circuit 2: Switch bank

There are several values and parts of code which can be enabled and disabled, but changing them requires the code to be recompiled and uploaded. To prevent this, Circuit 2 will have a bank of eight switches which can change Boolean values in the code during runtime. Such variables include whether or not to play sounds, send serial or to be controlled manually.

### Circuit 3: IR LED Mount Board

This board will mount 6 IR LEDs which surround a separate IR camera. A switch will allow the LEDs to turn on or off manually. These LEDs will be used to light up the arena and due to the nature of the IR camera returning the location of the four greatest IR sources, can assist in detecting packages.

## 3.2 Sensors

The sensors are another vital component to the correct operation of our robot. The sensors are required to be placed in such a way that will allow them to detect their environment accurately and relay this information to the Arduino. The following describe tasks that must be fulfilled and the sensors chosen to accomplish them.

### Obstacle Avoidance

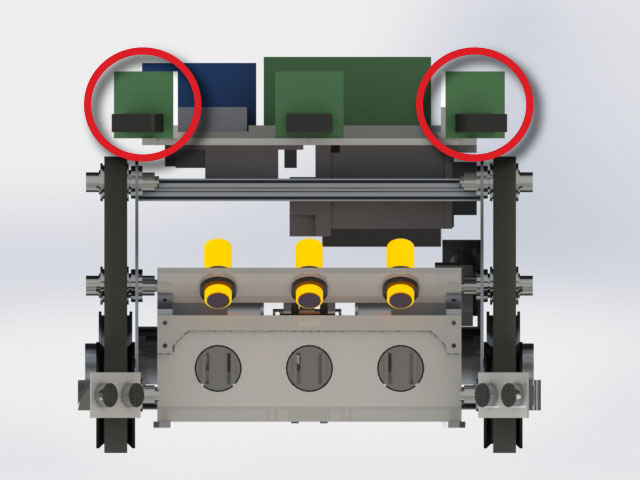
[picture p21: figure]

In order to navigate the arena, a combination of two medium and one long range IR sensors have been implemented for obstacle collision avoidance. IR sensors are much better suited to detecting obstacles as they have a narrower beam width and do not suffer from beam deflection.

The medium IR sensors were used for obstacle collision avoidance as they could operate efficiently with the range of 100-800mm. These sensors were mounted on the front of the robot and set at an angle of 35 degrees from forwards (facing inwards). See figure 9 for sensor position. This would allow the medium IR sensors to work in tandem with the ultrasonic sensors, allowing the robot to both detect obstacles and help distinguish packages.

Figure 9, Shows the location of the medium range IR sensors.

For to assist in avoiding poles, the long IR sensor was used for the functionality assessment. It was placed in line with the medium IR sensors at the front of the robot. The IR acts to fill in areas that are not detected by the medium IR sensors. Figure 10 indicates the location of the long range IR.

Figure 10, Shows the location of the long range IR sensor.

The IRs were required to be calibrated to allow the robot to know approximately how far obstacles are situated in relation to itself. This was done by measuring the signals from the sensor at varying distances and saving their value to the robot's configuration file.

### Package Detection

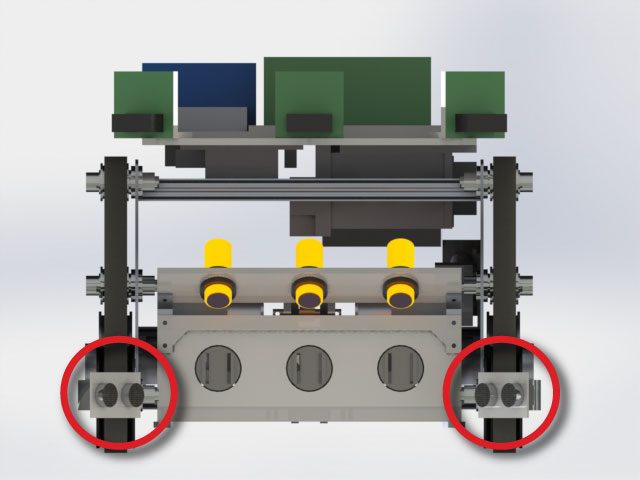
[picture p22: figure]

It is obvious that the robot must have the ability to detect packages in the arena that it may bring them on in a permanent fashion. To achieve this, the ultrasonic sensors provided were utilised. Ultrasonic sensors are much better at detecting packages due to their broad beam width and ability to detect cylindrical objects. Two ultrasonic sensors were mounted at the bottom of the robot in front of the tracks. By comparing the signal difference between the top mounted IRs and the bottom mounted ultrasonic, the robot is able to distinguish between obstacles and packages. The ultrasonic sensors were set at an angle of 40 degrees to allow broad sensor coverage for the front of the robot. The mounting for the sensors are shown in Figure 11. Unlike the IR sensors, the ultrasonic were not required to be calibrated as they operate on a function that takes into account the speed of sound which determines the distance based on the delay. Figure 12 shows all these sensors’ sight and their blind spots.

Figure 11, Shows the location of the ultrasonic sensors.

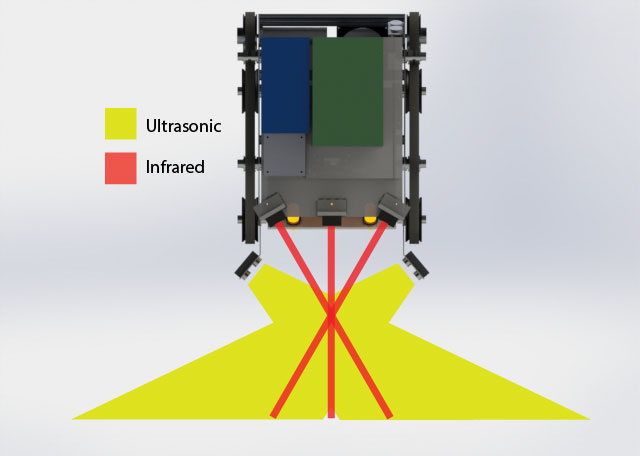
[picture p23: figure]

Figure 12, Shows the birds eye view of the sensor placement.

The reason the ultrasonic and IR sensors do not need to be straight above each other is due to the angle of the beam and the angle of the sensors. Since the ultrasonic has a beam width of 15 degrees, the IR sensors have been set to be pointing 15 degrees further forward (35 degrees rather than 50). This means that the IR beam will be travelling parallel with the ‘front edge’ of the ultrasonics’ edge. The two areas this could cause problems is directly in front of the robot (which is solved by having a forward-facing IR), and right next to the ultrasonic sensors, in which case is close enough that the robot should collect it anyway.

Because the ultrasonic and IR sensors can be noisy, the supplied IR camera will be used to assist. This has the ability to detect four IR sources and give you the x and y coordinates in the perspective of the camera, and possibly from the perspective of the robot in the arena. Since it will be used in conjunction with IR LEDs (see Circuit 3), the packages would reflect the IR waves and appear as the brightest spot on the camera as it would reflect more than the surrounding darker obstacles. It does have some drawbacks including the risk of interference from the opposition robot, which is why it is only a secondary method.

### Package Confirmation

Variable IR sensors will be used as on board package detectors as they had a simple true or false signal return. When packages are picked up by the magnets, the variable IR will trigger, allowing the robot to know the number of packages currently on board. These sensors are situated directly above the permanent magnets on the pickup module. This can be clearly seen in Figure 13.

### Distinguishing Bases

Figure 13, Shows the location of the variable IR sensors.

For the robot to detect the arena bases, the colour sensor must be implemented in the design. This sensor should be placed as near to the front of the robot as possible to allow for ease of detection. The exact location of this sensor is yet to be determined, but will likely be inside the Perspex shell of the pickup mechanism so that it is shielded from the ground.

### Navigation

Besides using the IR sensors for avoiding obstacles, the robot must also know where it is on the map for our design. The other two sensors that will be used for this purpose are the digital encoder (attached to the drive wheels) and the IMU. The digital encoder will simply be used to predict how far it thinks it has moved, and the rest of the sensors will confirm or update the position using Simultaneous Localization and Mapping (SLAM).

# 4.0 Software Design

## 4.1 Program Structure

As an autonomous robot, the code is complex and needs to be well structured. Before writing anything, the different modules were created in order to keep everything tidy and fulfil R5.4. The program was implemented primarily from a bottom-up approach, creating the low-level sensor and actuator functions, followed by a top-down approach. This meant the robot did not have to be physically built initially, besides plugging in the components on a temporary basis to test code.

Each module is written to be as independent from others as is reasonable, with a level of abstraction for other modules to reference. Their interfaces with other modules are demonstrated in Figure 14 while the support functions are used by most other modules. While much code for a map and SD card referencing have been written, they were not used in the functional assessment.

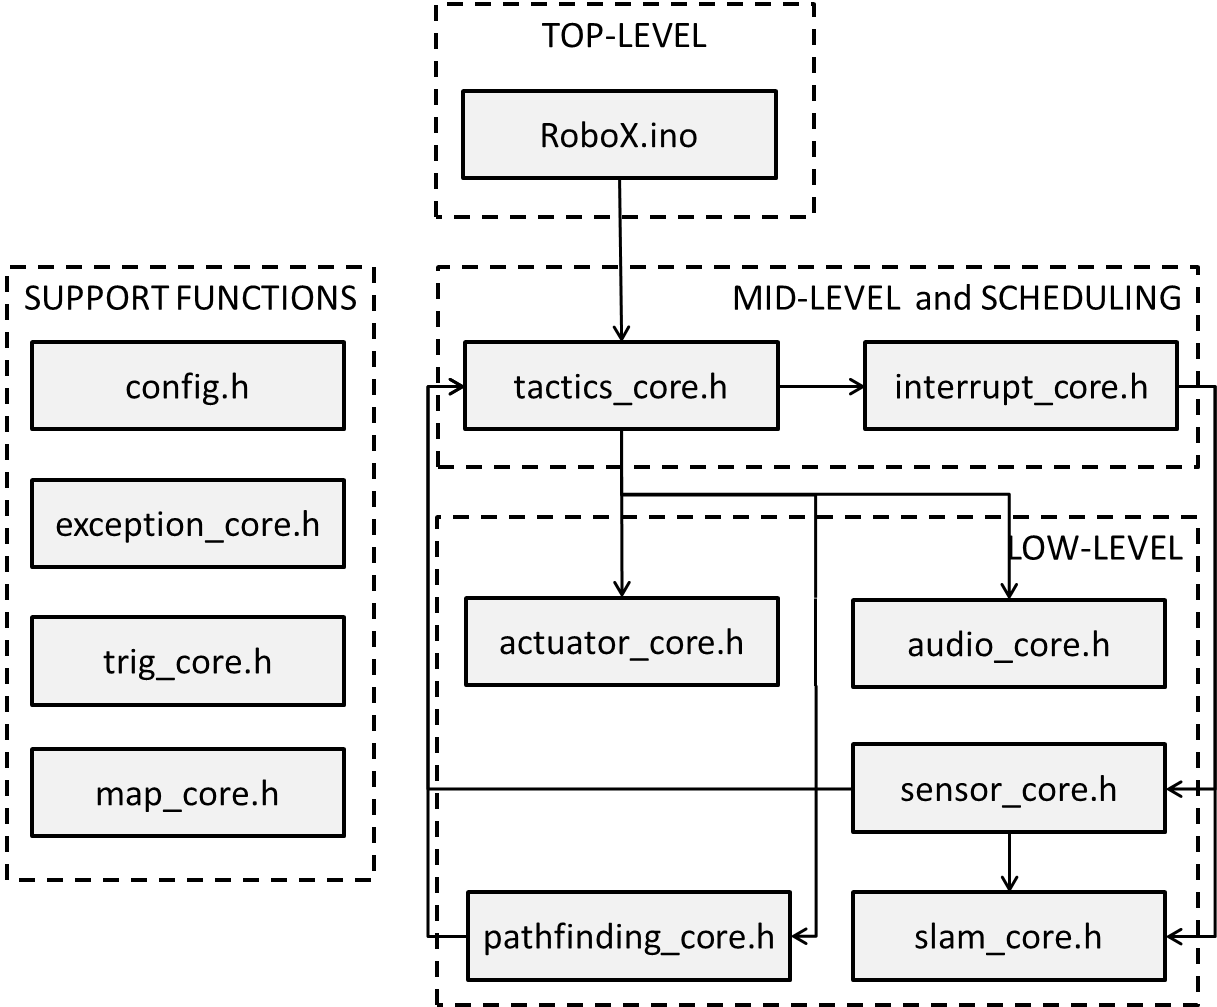
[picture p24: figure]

Figure 14, the files and how they interact

## 4.2 Support Functions

### config.h

To make adjustments to the robot simpler and all in one place, a configuration file was written. It contains no functions or classes, but only macros. This includes the components pin-out, sensor calibration and various program parameters. This file only has values that are subject to change, other macros are also defined in the relevant modules to keep the program clean. Several definitions are there to enable or disable various aspects of the program in order to save processing time. These include whether or not to print serial, play sounds or use the map.

### exception_core.h

The exception core is a design decision intended to make it easier to code ways around potentially crippling errors. It contains a class which is essentially an error flag with a wrapper. If there is some problem (such as the motors do not initialise), then it raises the flag and prints the error (or plays a sound). Another section of code detects the error and takes a different course of action. This is intended only for functionality issues rather than normal program operation such as detecting a base.

### trig_core.h

Since the intention of the program is to eventually use mapping and localization, trigonometric functions will be an essential set of tools. This module includes two classes and several macros for radian and degree conversions. The two classes are a two-dimensional Cartesian vector and a polar vector, and use overloaded functions to make it as easy to use as possible.

Since the vectors would added multiple times throughout the code, the efficiency of two different methods were compared. When adding two Cartesian vectors, it is simply a matter of adding components, but when adding two polar vectors, the sum can either be calculated directly or added as polar vectors. The comparison can be found in Appendix 4, which showed that converting to Cartesian coordinates, adding and converting back is more efficient than using trigonometric functions. This led to the decision to use Cartesian form as often as possible to make it even more efficient.

### map_core.h

Since both the SLAM and pathfinding will constantly be referring to a map, another module was created for it. Initially, a single file was going to be created on the SD card containing the map information, but there were going to be issues with reading, writing and particularly changing values in the map. Instead, each node (point) on the map is located in a different file which, although is slower on average, is more consistent in speed, and is much more versatile. The robot could theoretically map out any size of arena if the SD card is large enough.

## 4.3 Top-Level Design

Since the robot is autonomous and will have no human intervention (R1.1), the code must be as robust as possible, and have backup systems in case of failure. To accommodate this, there is a loop even higher than the main routine. There are a total of four ‘main loops’ which the program can fall into depending on the state of the robot. Each of these is found in tactics_core.h.

### Idle Loop

When the robot starts, each module is initialised and the program falls into the ‘idle’ loop. This is simply so that the robot can wait for user input that the round is starting. The robot will not fall back into this loop unless there is human intervention (the round has finished) or everything else has failed.

### Primary Loop

When the round has started, the program begins the Primary Tactic. Under normal circumstances, the robot will perform SLAM, pathfinding and high level decision-making. If there is any crippling error such as losing the SD card, then it will drop to the Secondary Tactic.

### Secondary Loop

This routine is meant to pick up packages with minimum complexity. This means there is no mapping or planning, but only on-the-spot decision-making. Since there is still a colour sensor, the robot is still capable of returning packages to base and avoiding the opponent’s base, the only disadvantage over the Primary Tactic is that it will be less efficient. It should be noted that this is the code that was developed for the functional assessment so that there is a fall-back for the Primary Tactic.

### Manual Loop

There is a fourth loop which has been implemented, and gives full control to the user. The user can send commands through the serial terminal to make the robot manoeuvre and move other actuators, and the terminal prints the sensor readings. This mode has been used extensively for testing, though will be less useful now that the development is focussed on the other tactics.

## 4.4 Mid-Level Design

Each of the main loops have the same basic structure - when the function (tactic) is called, it initialises relevant variables and sets the correct interrupt. This interrupt will read the sensors as well as performing other foreground tasks at regular intervals. After this, it enters the while loop containing background tasks. The idle loop and manual loop have no further design, as they simply wait for user input, so only the two autonomous loops will be discussed in this section.

### Primary Tactic

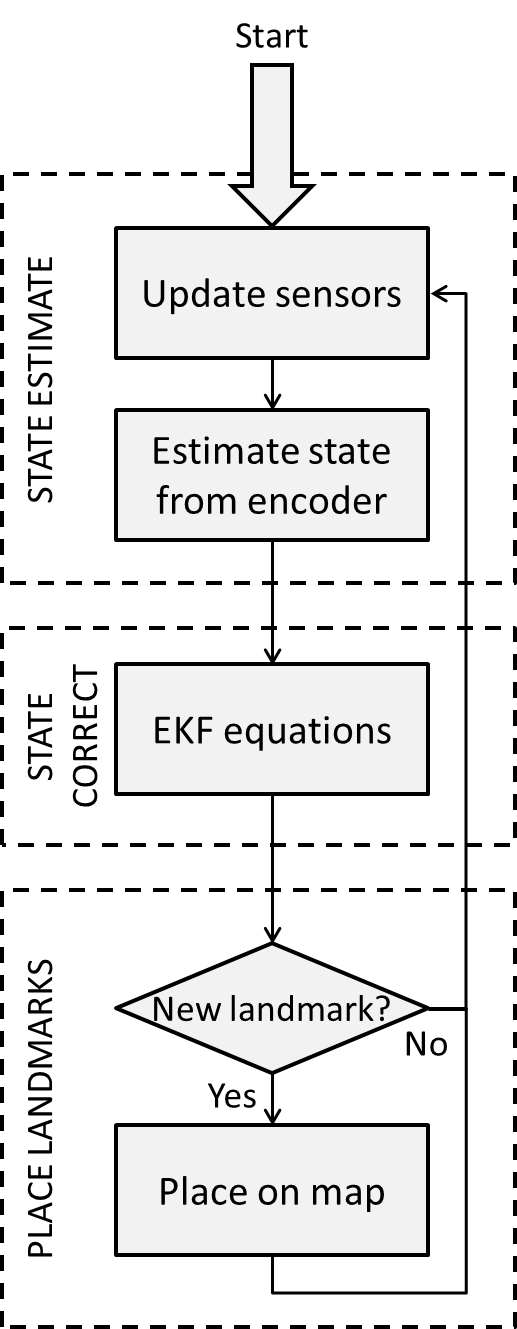
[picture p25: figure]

Because the Secondary Tactic was developed for the functional assessment, there are few completed parts of the program. The flow of the program has been written and is presented in Figures 15 and 16.

Figure 15 >, Primary Tactic foreground tasks

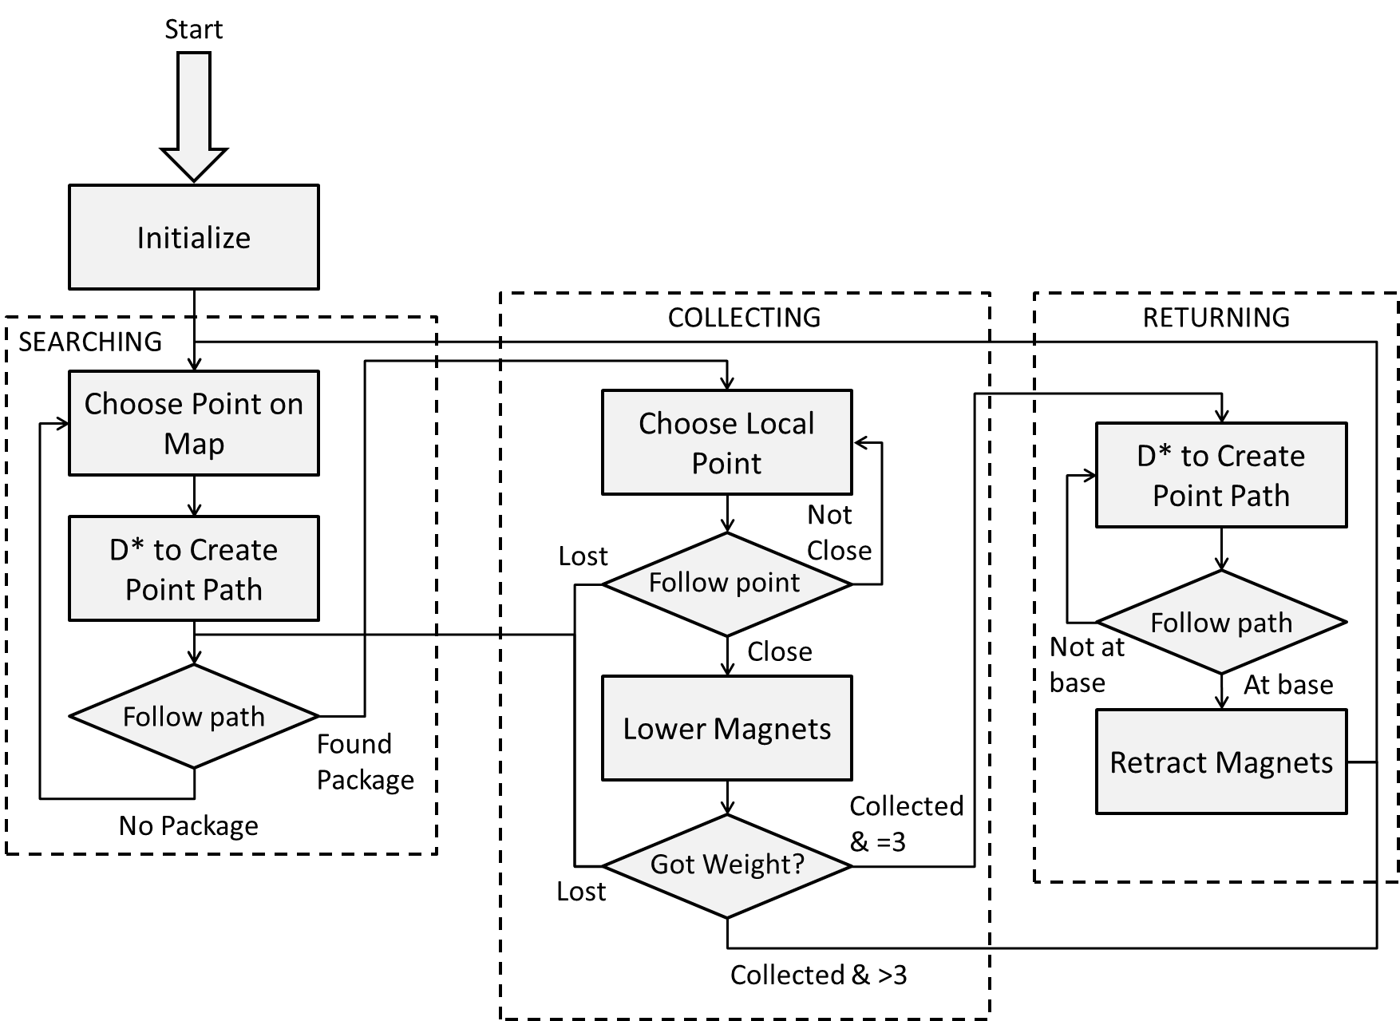
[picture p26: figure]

< Figure 16, Primary Tactic background tasks

### Secondary Tactic

The overall structure of this tactic is very similar to the primary one since it still intends on completing the same task. The main differences are that the navigation is basically random (whilst avoiding walls), and the robot will drop off packages whenever it can. Unlike in the previous tactic, no processing is done in the foreground, but only updating of the sensors.


Figure 17, Secondary Tactic background tasks

## 4.5 Low-Level Design

### actuators_core.h

Each of the different actuators (DC motors, servos, stepper motors) were implemented as classes. Since they each have different functions, they have similar, but not the same public functions. The stepper motors are given a relative position, servos are given an absolute position, and the DC motors are given a scaled speed and rotation.

It seemed that each time new electronics were installed the motors would have a different ‘zero’ velocity in code. Because in many cases this resulted in the robot moving backwards faster than forwards, a self-calibration routine was written. When the robot is initialized, it moves forwards a minute amount, moves backwards and centres the position.

### audio_core.h

Much effort was put into reading .wav files from the SD card, as well as playing audio in the foreground so that the robot could simultaneously play music and pick up packages. Unfortunately this could not be achieved. Instead, .rtttl files (ringtones) can be played, but only in the background, and not yet from the SD card.

### sensor_core.h

Although there are many different types of sensors, they were all implemented as classes with the same wrapper. This means that elsewhere in the code, the function calls are the same. Each of the range sensors (IR and ultrasonic) have five public functions:

- void initialize(parameters)
- void update(void)
- CartVec cart_read(void)
- PolarVec polar_read(void)
- bool is_valid(void)

In the foreground, each of the sensors is updated. This is a straight reading from the sensor with no processing. When this is done, a flag is set to say the value has not yet been processed. When the sensor needs to be read, it processes the value into another register, and decides whether or not the reading is valid based on the sensor type. If called again, the function will not process it a second time, but just returns the value. The reason there are two different types of reading is because they are useful in different scenarios. polar_read() returns a distance (mm) and an angle, whereas cart_read() returns the detected object position relative to the centre of the robot (in Cartesian coordinates).

As for the other sensors, they only have three public functions:

- void initialize(parameters)
- void update(void)
- type read(void)

These are the same as for the range sensors, only they return various different values depending on their function.

### pathfinding_core.h

The pathfinding method that will be implemented is D* Lite (or Dynamic A* Lite). This is a method of finding the fastest place between two nodes using heuristic values to optimise the speed (A*). Because the map is constantly being updated, there may be obstacles that were not taken into account. Instead of recalculating the route again, it recalculates it only based on what has changed (D*). This can be found in Appendix 6.

### slam_core.h

While none of the localisation has yet been implemented, some tests have been performed to find out some ways to optimise. There are two reasons for trying non-conventional methods for SLAM. Firstly, current methods are commonly done with a 2D rangefinding laser which returns a 2-dimensional array of distances, and that is unavailable within the budget – the comparatively crude and more discrete IR and ultrasonic sensors are all we have. Secondly, the landmarks that will be created will not just be used for localisation but also pathfinding, which is best done in a ‘grid’ method rather than list of obstacles.

# 5.0 Design Evaluation

## 5.1 General

#### R1.1 The robot will be fully autonomous ✔

#### R1.2 The robot will be controlled by the Arduino Mega ADK supplied ✔

#### R1.3 The robot shall be able to move, identify and collect packages ✔

#### R1.4 The robot shall operate until all 11 packages are claimed or the time limit is reached ✘

Currently, the robot can act fully autonomous with the provided Arduino Mega ADK. It can move around the arena and collect packages consistently. It is yet to be tested with collection of more than three packages as this requires returning to base to drop off the collected packages.

## 5.2 Identification

#### R2.1 The robot shall be able to identify food packages ✔

To test this functionality, an experiment was setup to observe the detection of packages within the arena. The packages were placed at 0, 30, and 60 degree angles on both sides of the centre line of the robot at a distance of 600 mm. The time taken to detect and retrieve the packages was measured, and it took an average time of 3.93 seconds when it was detected. It could not detect the packages at 60 degrees, but it found 90% of the other packages successfully. Results can be found in Appendix 3.

Based on the findings from this experiment, we can see that packages are easily detected and collected when they are at relatively small angles from the robot’s centre line. Beyond this the ultrasonic sensors are limited by their beam width and set angle. The robot will eventually detect and collect the packages in the arena at any position from the centreline, but it requires the robot to approach from a shallower angle. It should also be noted that the robot produced false detections during the experiment when driving close to the arena walls. It is suspected that the skirting around the arena gives false positives but this needs to be investigated further.

#### R2.2 The robot shall be able to identify obstacles it cannot move over ✔

This was implemented using the medium and long range IR sensors as discussed in the previous report. As a result, the robot performed adequately during the functionality assessment. Its ability to detect poles still lacks accuracy and consistency and should be significantly improved before the final assessment.

#### R2.3 The robot shall be able to distinguish home HQ and the opposition HQ ✘

The colour sensor example code functioned at an acceptable standard, but would not operate in conjunction with the rest of the program. This has not yet been solved, so the robot cannot distinguish between bases. It should be noted that the robot can distinguish the bases as a side-effect of the digital IR sensors – when on a base, all three sensors ‘detect a package’ due to the change in specularity.

#### R2.4 The robot should rely on a range of navigational sensors ✔

As discussed previously, the robot uses four different types of sensors based on their varying specifications. The range of sensors used is expected to increase by about two times.

## 5.3 Movement

#### R3.1 The robot shall be able to move over obstacles at least 25mm in height ✔

The 3D printed wheels discussed in Section 2 give the robot a ground clearance of over 25mm. They were designed this way and measured using Solidworks.

#### R3.2 The robot shall be able to fit through gaps of at least 500mm in width ✔

When placing the robot in between two walls, it successfully drives though the gap.

#### R3.3 The robot shall be able to manoeuvre around obstacles it cannot move over ✘

The robot can manoeuvre around and follow walls. Unfortunately due to the false detection of packages, it occasionally turns towards and collides with the walls. The robot, while it can detect cylindrical object, currently does not attempt to avoid them.

#### R3.4 The robot shall not leave the designated arena during the competition ✔

It is impossible for the robot to climb the walls.

#### R3.5 The robot should not get stuck in any algorithmic loops for longer than 1 minute ✘

No watchdog timer or other method has yet been implemented to avoid this. When mapping and D* are functional, it may not even be necessary to use a timer.

## 5.4 Collection

#### R4.1 The robot shall be able to pick up a package so that it is under the robot’s control ✔

At this point the design can collect packages fast and effectively, as confirmed in the functionality assessment, and discussed under R2.1.

#### R4.2 The robot shall have a way of carrying, at most, three packages without hindrance ✘

Three packages are able to be picked without trouble. The tilt operation has not yet been implemented, so it is unable to prevent the packages from interfering with level obstacles.

#### R4.3 The robot shall not collect any packages within the opposition’s HQ ✘

The tilt operation has not been implemented and thus will collect packages in the opposition’s HQ.

#### R4.4 The robot should be able to release any packages it has on-board to HQ (Erogenous Zone) ✘

Much work was put into a release mechanism, as discussed in detail previously, but is unable to release more than one package. Minor developments and fine tuning is required to get enough force on the magnets.

#### R4.5 The robot should be able to pick up packages in any orientation and any part of the map ✘

The magnets attach the packages in any orientation, but is unable to pick up packages against a wall.

## 5.5 Construction

#### R5.1 The cost of additional items shall not exceed $50 (except for R5.2) ✔

The additional items as priced in Appendix 5 sum to $36.20.

#### R5.2 Each member shall design their own PCB for use on the robot, not exceeding $5 ✔

While the circuits haven’t yet been created, they have been designed, and are within budget.

#### R5.3 The robot should be built with less than 200g of 3D printer plastic. ✔

The four 3D printed wheels, each printed in two halves weighed a total of 152 grams.

#### R5.4 The robot shall be easy to maintain and disassemble ✔

By mounting all the circuit boards on a single sheet of perspex, it allowed for ease of total removal from the robot by the removal of the three mounting screws. For simple rewiring, the quick release with its swivel design could allow access to all the circuit boards in 12 seconds.

## 5.6 Safety

#### R6.1 The robot shall not cause any deliberate damage to anything or anyone ✔

#### R6.2 The robot shall have an accessible ‘off’ switch ✔

#### R6.3 The robot shall use the battery safety circuit provided ✔

The on/off switch and battery safety circuit were both used, and the switch was mounted at the back of the robot so it could easily be accessed. It will be necessary in the final assessment to relocate the switch as it could be disabled by the opposing robot.

# 6.0 Future Development

## 6.1 Mechanical Development

### Locomotion

The tracks stay on the majority of the time but still come off occasionally, so this will need further development. An extra bearing will be added to support and help guide the track on the bottom of the robot. Consideration are also being taken for adding a spring to the bearing to account for when that section of the track goes over a bump.

### Pickup Mechanism

The pickup mechanism needs fine tuning to make sure all the force is transferred to the magnets. This will be done by reinforcing the structure of the mounts and by connecting all the magnets together. For a greater force on the magnets two rubber bands may be added. This will give more force on the back the stroke of the mechanism where it needs the greatest force. When extending the magnets back out the mechanism will put energy into the rubber bands.

Having the pickup mechanism rotate up and down design also has to be finalised and implemented. At this stage two servos will be mounted above to raise and lower it.

A limit switch is needed to tell when the stepper motors have rotated around past the point of knocking of the packages. This will ensure the packages have indeed disconnected from the robot.

## 6.2 Electrical Development

Currently based on the sensor and circuit design, the robot functions on a basic level. It has the ability to navigate most obstacles and detect packages the majority of the time. It is now necessary to improve the reliability of package and obstacle detection. There are a number of potential design paths that we are currently considering adding or modifying for environment detection and they are discussed in brief below.

### Sonar

If a central mounted Sonar sensor was used instead of the long range IR that is currently utilised on the robot would be better at detecting poles. The advantage is that it produces a large beam width (similar to the ultrasonic sensors), and ‘fill in’ the whole blind spot in front of the robot. They would, however, be much less useful for mapping as there would be a large range of points that a value could represent. They are better for determining if something is detected rather than where it is.

### Swivel mounted IR

Because the IR sensors show a limited selection of the environment, it would be possible for one or two IRs to be mounted on a servo. These motors could be driven back and forth to produce a sweeping motion for the IR sensors. An array of values could be produced from this, but could potentially be more processor intensive. The other disadvantage is that the IR would only see each point once every one or two seconds.

### Side mounted IR

This would give a permanent view of a limited spot, almost the opposite of the swivel mounted IR. This would be good to help prevent collision from turning into walls from the side, as it would never be ‘looking away’, but only works because the majority of obstacles are large.

## 6.3 Software Development

Currently the robot is just able to fulfil the requirements of the functionality assessment, but there are still five specifications which need to be fulfilled by the software - over 50% of the remaining requirements.

### Final Sensors

Several of the requirements would be resolved by getting the remaining sensors functioning. The only sensors that do not currently work are the I²C sensors. Each of the example codes work, but none function when implemented with the rest of the code. Some test has shown it is not conflicting libraries, but it may be due to the power electronics involved.

The IMU will have additional issues as well, since the pickup mechanism’s permanent magnets will interfere significantly with the magnetometer.

### Tactics

Neither the Primary or Secondary tactics are currently fully implemented, each of which will take a significant amount of time. The secondary tactic has been written just well enough for the functionality assessment, but still needs much work before it can fulfil the specifications. Even though it is secondary, it will still be written and tested so that it works well so there is a fall-back if the primary does not work. This was intended to be fully complete by this time, so it is very possible there will not be sufficient time to accomplish the full SLAM and pathfinding. This is not a huge problem because even with just the secondary tactic the robot will achieve each specification.

# Contribution Statements

### JACK

- Design and build of electrical module
- Circuit 1 design
- Report electrical design section
- Proof reading
- Report formatting

### PETER

- Software design and implementation
- Circuit 2 design
- Part sourcing
- Report software design section
- Report formatting

### RYAN

- CAD modelling/drawing
- Pickup mechanism design, calculations, Matlab coding and build/machine (85 hours )
- Material/Parts sourcing
- Circuit 3 design
- Report mechanical design section
- Report formatting

# Appendix 1 – Matlab Code and Derivation

clear, clc

close all

force_required = 150; %N

motor_torque = 1.76*2; %Nm

radius_gear = 0.010; %needs to be more then half the distance of our tavel

radius_rod = 0.030;

off_set = 0.050;

% 0 10 20 30 40 50 60 70 80 90 100 110 120

b_length = [61.3 63.2 64.8 66.1 67.4 68.6 69.4 70.5 70.6 70.6 70.5 69.4 68.6 67.4 66.1 64.8 63.2 61.2 60 58 56.4 54.7 53.6 52.3 51.4 51 50.7 51 52.3 53.6 54.7 56.4 58 60 60.8 61.3];

b_angle = [9.5 9 8.4 7.6 6.6 5.3 4.0 2.7 1.5 0 2.7 4.0 5.3 6.6 7.6 8.4 9 9.5 9.6 9.4 8.9 8.1 7.2 5.6 4 2.2 0 2.2 4 5.6 7.2 8.1 8.7 9 9.2 9.5];

a = 1;

for i = 1:1:36 ;

angle_c(i) = asind(sind(i*10+90)*0.05/(b_length(i)/1000));

end

for i = 1:1:36

force_b(i) = motor_torque*cosd((angle_c(i)))/0.01;

end

for i = 1:1:36

torque_b(i) = force_b(i)*b_length(i)/1000;

end

for i = 1:1:36

force_rod_per(i) = torque_b(i)/0.03;

end

for i = 1:1:36

force_rod(i) = force_rod_per(i)*cosd(b_angle(i));

end

for i = 1:1:36

force_needed(i) = 150*3;

end

plot(force_rod,'r')

grid on, hold on

plot(force_needed)

axis([0 37 0 900])

title('Force applied to magnets')

xlabel('Motor angular displacement')

ylabel('Force applied to magents')

legend('Force applied','Force needed')

motor_force = motor_torque / radius_gear

applied_force = motor_force * (off_set / radius_rod)


# Appendix 2 – Circuit Schematics and PCB Diagrams


# Appendix 3 – Package Detection


Test # | Centre line | 30 deg anti | 60 deg anti | 30 deg clock | 30 deg clock
1 | 3.88 | 3.80 | Not detected | NA | Not detected
2 | 4.00 | 3.96 | Not detected | NA | Not detected
3 | 3.90 | 3.86 | Not detected | 3.96 | Not detected
4 | 3.95 | 3.93 | Not detected | NA | Not detected
5 | 3.90 | 3.82 | Not detected | 4.08 | Not detected
6 | 3.92 | 3.80 | Not detected | 3.91 | Not detected
7 | 4.04 | 3.88 | Not detected | 3.93 | Not detected
8 | 4.14 | 3.84 | Not detected | 3.80 | Not detected
9 | 3.91 | 3.93 | Not detected | 4.08 | Not detected
10 | 3.64 | 4.13 | Not detected | 4.00 | Not detected
Average | 3.93 | 3.90 | Not detected | 3.97 | Not detected

# Appendix 4 – Efficiency Tests


Since the majority of vector addition will be adding an offset to the sensor, the offset can be saved in its Cartesian form. This would imply one fewer conversions.

| Polar | Cartesian | Difference | Efficient Cartesian | Difference
Add, Subtract | 4 | 2 | +2 | 2 | +2
Multiplication | 8 | 6 | +2 | 5 | +3
Division | 1 | 1 | 0 | 1 | 0
Absolute Value | 1 | 0 | +1 | 0 | +1
Tan Inverse | 0 | 1 | -1 | 1 | -1
Sine | 1 | 2 | -1 | 1 | 0
Sine Inverse | 1 | 0 | +1 | 0 | +1
Cosine | 1 | 2 | -1 | 1 | 0
If Statement | 1 | 1 | 0 | 1 | 0
Square Root | 1 | 1 | 0 | 1 | 0

# Appendix 5 – Bill Of Materials

## Bill Of Materials (Provided)

Item | Quantity | Total Cost (NZ dollar)
Aluminium plate | 2 | 32.00
Aluminium extrusion | 4 | Not priced
Sensor Circuits | 4 | Not priced
Arduino Mega ADK | 1 | 60.00
Lithium Battery | 1 | Not priced
Ultrasonic Sensor | 2 | 2.00
Medium Infrared Sensor | 2 | 38.00
Long Infrared Sensors | 1 | 17.00
Cables | NA | Not priced
3D Printed Wheel | 4 | Not priced
Smart Servo | 1 | 50.00
DC motor | 2 | 106.00
Drive Wheel | 2 | Not priced
Bearing (29mm) | 16 | Not priced
M3 Cap Screws | NA | Not priced
M8 Cap Screws | 10 | Not priced
Aluminium 15mm 40x100 | 1 | 5
Aluminium 5mm 120x100 | 1 | 10
Aluminium 2mm 300x200 | 1 | 5
Steel rod 1/4 inch 200mm | 1 | 1
Steel rod 10mm 100mm | 1 | 0.5
Spring 20mm compressive | 1 | 0.1
Perspex 10mm 200x350 | 1 | Not priced
Perspex 4mm 200x150 | 1 | Not priced
M3 | 40 | 4
M5 | 4 | 0.75
Geared Stepper | 2 | 30
Digital IR | 3 | 15

## Bill of Materials (Additional)

Item | Quantity | Total Cost (NZ dollar)
SD Storage Card | 1 | 4.09
SD Reader | 1 | 2.11
Permanent Magnets | 3 | 30.00
Total Cost | | $36.20

## Bill Of Materials (Circuit 1)

Item | Quantity | Cost (NZ dollar)
1000 uF/ 25V electro cap | 1 | 0.22
10 uF/ 25V electro cap | 1 | 0.04
100 n cap | 1 | 0.05
47 n cap | 1 | 0.40
IC LM386 | 1 | 0.08
10k variable resistor | 1 | 0.33
10 Ω resistor | 1 | 0.02
1 W speaker | 1 | 0.51
Total Cost | | $1.65

## Bill Of Materials (Circuit 2)

Item | Quantity | Cost (NZ dollar)
SW DIP-8 | 1 | 2.51
RJ45 8P8C jack | 2 | 0.50
Resistor 10K | 8 | 0.02
Total Cost | | $3.67

## Bill Of Materials (Circuit 3)

Item | Quantity | Cost (NZ dollar)
IR LED | 6 | 3
220 Ω resistor | 6 | 1
Header pin | 2 | 0.1
Switch | 1 | 4
Total Cost | | $8.10

# Appendix 6 – D* Lite (Pseudocode)

procedure CalcKey(s) {

return [min(g(s), rhs(s)) + h(s_start, s) + km, min(g(s), rhs(s))];

}

procedure Initialize() {

U = []

k_m = 0;

for all s in S rhs(s) = g(s) = inf;

rhs(s_goal) = 0;

U.Insert(s_goal, [h(s_start, s_goal); 0]);

}

procedure UpdateVertex(u) {

if (g(u) != rhs(u) AND u in U) U.Update(u, CalcKey(u));

else if (g(u) != rhs(u) AND u not in U) U.Insert(u, CalcKey(u));

else if (g(u) = rhs(u) AND u not in U) U.Remove(u);

}

procedure ComputeShortestPath() {

while (U.TopKey() < CalcKey(s_start) OR rhs(s_start) > g(s_start))

u = U.Top();

k_old = U.TopKey();

k_new = CalcKey(u));

if(k_old < k_new)

U.Update(u, k_new);

else if (g(u) > rhs(u))

g(u) = rhs(u);

U.Remove(u);

for all s in Pred(u)

rhs(s) = min(rhs(s), c(s, u) + g(u));

UpdateVertex(s);

else

g_old = g(u);

g(u) = 1;

for all s in Pred(u) union {u}

if (rhs(s) = c(s; u) + g_old)

if (s != s_goal) rhs(s) = min_s'_Succ(s) (c(s, s') + g(s'));

UpdateVertex(s);

}

procedure Main() {

s_last = s_start ;

Initialize();

ComputeShortestPath();

while (s_start != s_goal)

/* if (rhs(s_start) = inf) then there is no known path */

s_start = arg min_s'_Succ(s_start) (c(s_start, s') + g(s'));

Move to s_start;

Scan graph for changed edge costs;

if any edge costs changed

k_m = k_m + h(s_last, s_start);

s_last = s_start;

for all directed edges (u, v) with changed edge costs

c_old = c(u, v);

Update the edge cost c(u, v);

if (c_old > c(u, v))

rhs(u) = min(rhs(u), c(u, v) + g(v));

else if (rhs(u) = c_old + g(v))

if (u != s_goal) rhs(u) = min_s'_Succ(u)(c(u, s') + g(s'));

UpdateVertex(u);

ComputeShortestPath();

}

S Koenig, M Likhachev. (2002). ‘Fast Replanning for Navigation in Unknown Terrain’ [online]. Available: https://www.seas.upenn.edu/~maximl/files/dlite_tro05.pdf

# Appendix 7 – Drawings For Mechanism Systems

Robocup Progress Report 2 Group 10

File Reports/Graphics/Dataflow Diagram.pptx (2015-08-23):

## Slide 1

SENSORS

Range

Colour

Packages

PROCESSING

Localization

Tactics and Decisions

ACTUATION

Movement

Collection

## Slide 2

MID-LEVEL and SCHEDULING

LOW-LEVEL

TOP-LEVEL

RoboX.ino

SUPPORT FUNCTIONS

config.h

exception_core.h

trig_core.h

map_core.h

tactics_core.h

actuator_core.h

interrupt_core.h

audio_core.h

sensor_core.h

pathfinding_core.h

slam_core.h

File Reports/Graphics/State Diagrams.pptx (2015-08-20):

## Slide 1

Start

Search For Packages

Package
Collected

Found
Package

Collect Package

Packages
Offloaded

Got 3
Packages

Return to HQ

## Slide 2

Start

Follow Wall (Clockwise)

Package
Collected

Found
Package

Collect Package

Packages
Offloaded

Got 3
Packages

Follow Wall (Anti-clockwise)

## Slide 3

Start

Search For Packages

No

Found
Package

Heavier?

Package
Collected

Yes

Remove Lightest and Collect

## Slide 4

Start

Initialize

SEARCHING

Choose Point on Map

D* to Create Point Path

COLLECTING

Choose Local Point

Lower Magnets

RETURNING

D* to Create Point Path

Retract Magnets

Not
Close

Lost

Follow point

Follow path

Close

Not at
base

At base

Follow path

No Package

Found
Package

Collected
& =3

Lost

Got Weight?

Collected & >3

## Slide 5

Start

STATE ESTIMATE

Update Sensors

Estimate State from Encoder

STATE CORRECT

EKF Equations

PLACE LANDMARKS

New landmark?

Place on Map

No

Yes

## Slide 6

Start

Initialize

SEARCHING

Avoid walls

Found package?

COLLECTING

Choose Local Point

Follow point

Lower Magnets

RETURNING

Avoid walls

Retract Magnets

At base?

Yes

Lost

Not
Close

At base?

No

Not at
base

At base

Yes

Close

No

Got Weight?

Collected & >3

Collected
& =3

Lost

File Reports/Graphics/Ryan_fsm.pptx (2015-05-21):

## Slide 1

Start state
- Determine headquarters colour and other teams headquarters colour

Colour of headquarters registered

Return to headquarters state
- Use information provided by path finding to get our headquarters
- Colour detected

Colour of headquarters recognized

Dropping of packages state
- Lower magnet assembly
- Drive to stepper servos
- Retract to stepper servos
- Raise magnet assembly

Path finding state
- Update map
- Look for packages
- Decide where to drive next

Locate package

Get package state
- Align package with free magnet

Aligned to attach package

Attach package state
- Lower magnet assembly
- Drive into package
- Raise magnet assembly
- Record package onboard and magnet used

Three packages attached

Less then three packages on board
OR package was not picked up

Packages detached

Some packages still attached

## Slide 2

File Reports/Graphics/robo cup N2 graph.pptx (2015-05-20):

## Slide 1

Structure

Battery

DC motors

Controller

Hall effect
sensors

IR sensors

Legend:
Mechanical interface
Electrical interface
Program interface

Servos

Color sensor

Track
locomotion

Prong storage
system

Power
distribution
circuit

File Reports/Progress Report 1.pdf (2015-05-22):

### UN I VERSI T Y O F CAN T ERB U RY

# ROBOCUP PROGRESS REPORT 1

### GRO U P 10

Jack Hendrikz
Peter Nicholls
Ryan Taylor

## 22 May 2015

Robocup Progress Report 1 | Group 10

TABLE OF CONTENTS

0.0EXECUTIVE SUMMARY

A search and retrieval robot must be designed for the 2015 Robocup challenge. This robot must autonomously search for packages in an arena and return them to its HQ. It was determined that the ideal concept design for this challenge is Concept One as it has a robust design with a retrieval method that can pick up the packages in varying orientations using magnets. It also employs a sophisticated path finding program allowing the robot to navigate the arena with minimal difficulty, therefore ideally suiting it for efficient package retrieval.

### 1.0 INTRODUCTION

In this year’s Robocup Zombie apocalypse, teams will design robots that search autonomously for food packages. The robot will compete in the arena against another robot for these packages. The battle will take place in a hostile environment, including unmoveable obstacles, walls, and a series of rough sections of ground all unknown to the robot. The robot will need to return the food packages to the team’s headquarters. Food packages consist of cylindrical weights made from steel and will be placed in both easy and hard to reach places.

Three concepts will be presented and evaluated to overcome this design problem. The three main areas for design will be the navigational sensors, locomotion and tactics. A merit table will be presented and a final recommendation will be suggested.

### 2.0 REQUIREMENTS SPECIFICATION

### 2.1 GENERAL

R1.1 The robot will be fully autonomous
R1.2 The robot will be controlled be the Arduino Mega ATK supplied
R1.3 The robot shall be able to move, identify and collect packages
R1.4 The robot shall operate until all 11 packages are claimed or the time limit is reached

### 2.2 IDENTIFICATION

R2.1 The robot shall be able to identify food packages
R2.2 The robot shall be able to identify obstacles it cannot move over
R2.3 The robot shall be able to distinguish home HQ and the opposition HQ R2.4 The robot should rely on a range of navigational sensors

### 2.3 MOVEMENT

R3.1 The robot shall be able to move over obstacles at least 25mm in height R3.2 The robot shall be able to fit through gaps of at least 500mm in width
R3.3 The robot shall be able to manoeuvre around obstacles it cannot move over R3.4 The robot shall not leave the designated arena during the competition
R3.5 The robot should not get stuck in any algorithmic loops for longer than 1 minute

### 2.4 COLLECTION

R4.1 The robot shall be able to pick up a package so that it is under the robots control R4.2 The robot shall have a way of carrying, at most, three packages without hindrance
R4.3 The robot shall not collect any packages within the opposition’s HQ
R4.4 The robot should be able to release any packages it has on-board to HQ
R4.5 The robot should be able to pick up packages in any orientation and any part of the map

### 2.5 CONSTRUCTION

R5.1 The cost of additional items shall not exceed $50 (except for R5.2)
R5.2 Each member shall design their own PCB for use on the robot, not exceeding $5 R5.3 The robot should be built with less than 200g of 3D printer plastic.
R5.4 The robot shall be easy to maintain and disassemble

### 2.6 SAFETY

R6.1 The robot shall not cause any deliberate damage to anything or anyone R6.2 The robot shall have an accessible ‘off’ switch
R6.3 The robot shall use the battery safety circuit provided

### 3.0 DESIGN SPACE AND CONCEPT GENERATION

While there are many ways to go about fulfilling the requirements, the robot will always have sensors, some form of actuation and some sensible way of linking the two. Figure 1 demonstrates how the three blocks interact with each other in the context of the Robocup robot. All of the aspects of the system shown in the figure will be discussed in this section with the exception of the collection method, as this is highly depended on the rest of the proposed concept. It will instead be discussed in Section 4.0.


Figure 1: Dataflow within the robot

### 3.1 NAVIGATION SENSORS

A mechatronic system relies on interacting with the world around it; it uses sensors to see and give feedback to decide what the system should do. The robot we will design has a wide range of sensors available. The following sensors are provided:

- 2 × Ultrasonic Rangefinder
- 1 × Infrared (Short range)
- 1 × Infrared (Medium range)
- 3 × Infrared (Variable range)
- 1 × Infrared camera
- 1 × Sonar
- 1 × Colour detector
- 1 × Weight sensor
- 2 x Limit Switch
- 1 x IMU

Navigation
To navigate around the arena, sensor feedback will be needed to give distances to objects around the robot. Ultrasonic and IR sensors give distance feedback ranging from 40mm to 5000mm. IR gives close to medium range with a small beam angle and ultrasonic gives medium to long range with a large beam angle. If either was used individually, it would work but be unreliable in some situations. Using both types of the sensors at the same time will help to give the microcontroller reliable results in terms of distance and angle. The downside to the ultrasonic is it has a 100ms measurement cycle compared to the IR 30ms measurement cycle. In addition to these two sensors, the sonar is also capable of measuring distances although it is much less consistent. While we could use the limit switches for navigation, they could be put to better use inside the robot.

An IR camera is also supplied, this camera can see IR or fire sources. Since there are no fires in the arena, the only source would be IR from the other robot provided they have used IR sensors. Knowing where the other robot would be useful, however the camera would only detect the opposition robot when it was pointing its IR sensors at our camera.

A powerful IMU is supplied which has a three axis accelerometer, three axis gyroscope, barometer and compass. Complete control is given over the different sensors allowing any sensor on the IMU to be used or not used. For navigating the arena the compass could be very useful giving a heading for the robot and the accelerometer would be good to sense if the robot was started moving or suddenly stopped. However, these sensors would have to be merged in some way otherwise the nearest motor would always be North.

Package Detection
For detecting the packages, several methods could be used, but the most reliable would be a sensor fusion of two distance sensors. Nothing in the arena is as short as the packages, meaning that if there is a difference in length between a high and a low sensor, then there must be a package. This can be arranged so that it can detect packages if they’ve fallen over as well, as seen in Figure 2.


Figure 2: Package detection using sensor fusion

In order to comply with R4.2, the robot needs some way of telling how many packages are on board. The limit switches supplied would be ideal for this job, although it would be very important to get the switch positioned well.

A weight sensor supplied is able to measure a load itself. It uses a strain gauge to measure the weight. More points are awarded for the heavier packages. This means the heavier packages are more valuable when picking them up. With the limitation of only having three packages on board having three light compared to three heavy could be a loss of half the points. Implementing the sensor mechanically to have the correct reading will be quite hard as the picking up or holding system will have to be suspended by the sensor. This sensor is digital, with serial output.

Finding HQ
Instead of just ‘remembering’ where HQ is, the colour sensor could be used for detecting whether the robot is in a base or not, and further to detect which base it is in. It is important to be able to determine the bases apart for requirements R2.3 and R4.3. The robot cannot pick up packages from the other team’s headquarters so the robot will need to prevent its mechanism for package retrieval. Once three packages are on-board the robot will need to return to HQ to drop them off. The colour sensor will confirm that it has arrived before it starts to drop them off.

### 3.2 LOCOMOTION

In industry, robots have a large range of locomotion options that vary depending on the surrounding environment and the tasks that the robot must undertake. The designed robot must have the ability to manoeuvre around its environment in a way the packages can be picked up efficiently and quickly. It will be constructed to allow it to tackle obstacles such as ramps, walls and the other robot whilst in the arena. This can be achieved through both a reliable and robust locomotion method and chassis design. There are two locomotion methods that can be implemented on the robots in this arena search and retrieval scenario, wheels and tracks.

Wheel Locomotion
Wheels are a common occurrence in mechatronic designs as they allow for simple locomotion by being actuated by the motors directly. They have a variety of steering methods from differential steering (driving like a tank) to crab driving where each wheel is driven separately. Wheels can provide a much faster robot as there is less power required to drive them in comparison to tracks.

Track Locomotion
Tracked robots fair far better on uneven terrain due to the traction advantages as a result of increased surface area and low ground pressure. They are common on robots that operate out in the field as they can handle a wide range of terrain challenges that could not be tackled easily by a wheeled design. Turning can be achieved by slowing or reversing one of the tracks to enable pivoting on the spot.

Locomotion Comparison
The main issues faced using a wheel locomotion design is the lack of manoeuvrability. The turning of the robot would be tricky to construct as only two DC motors are provided to drive the robot. This means that a complex driving system would have to be designed in order to either pivot the front wheels for turning. Alternatively the robot could employ skid steering which is very unreliable for the robot which needs to know its position at all times. Wheels also struggle to traverse uneven terrain as they lack traction without a suspension system or large tyres. Tracked robots generally have a more complex design and can suffer from a lack of speed since more power is required to drive the tracks. Using the traction belts provided with the robot, the belt must be kept taught to prevent slip of the motor and a loss of driving ability.

Overall tracks appear to be the best method of locomotion as they will allow the robot to manoeuvre around the arena’s terrain at a reasonable speed whilst maintain stability. Using 3D printed drive wheels for the tracks will allow our group to optimise the performance of our tracked robot design by increasing torque and applied tension to the belt.

Chassis Design
The chassis must be built in such a way that the robot will be stable, light and allow for maintainability. To improve stability, the centre of mass must be as central and as low to the ground as possible. This will reduce the risk of the robot potentially tipping over and becoming stranded. Another key aspect to chassis design is weight as this will not only help provide traction via the tracks, but can also effect the speed at which the robot can manoeuvre at. Ideally a balance must be struck to allow a fast travelling tracked robot with a good amount of traction to scale obstacles in the arena. The chassis design should also take into account other components such as batteries, sensors and how easily they can be accessed and rewired during the construction and testing of the robot.

The chassis provided is constructed from sheet metal and aluminium support beams. It is a very good all-round chassis with a large number of mounting holes, although inverting it would significantly increase the stability. Doing this would require modification to the drive mechanism and 3D printed wheels, but these problems are outweighed by the benefits. A lighter and more compact chassis could be designed given enough time and money, but we believe this chassis will be fit for purpose for our robot construction.

### 3.3 TACTICS AND NAVIGATION

Unlike previous years, our robot is required to return the food packages to the headquarters. This significantly increases the complexity of the problem, and leaves essentially two solutions (each with subsets). The robot must:

1. Have some way of reliably returning to the headquarters, or
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

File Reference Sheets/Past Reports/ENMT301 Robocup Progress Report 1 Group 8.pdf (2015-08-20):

# RoboCup Progress Report 1

Matt Young, Hamish Black & Chris MacEwan | Group 8

Contents

# 1. Executive Summary

This report details the design process of Team 8 in the 2014 RoboCup Competition. For the competition, each team must build a robot that can navigate an arena to collect food packages. Hardware and software constraints, in addition to the project brief, were used to create a framework of specifications for the robot. Brainstorming within these specifications produced a variety of different methods for each aspect of the robots performance, which were used to develop a final set of three concepts. The three concepts were: a street sweeper which scoops packages into a holding bay; a robot which runs over the packages and forces them onto a set of parallel rails for storage; and a magnet which latches on to target packages and drops them into a storage bay. These three concepts were evaluated on a number of criteria including cost, reliability and power requirements. The magnet concept was chosen as final design to proceed with as it best fulfilled the evaluation criteria.

# 2. Introduction

Every year, 2nd Pro Mechatronics students at the University of Canterbury compete in the Canterbury RoboCup Competition. Students are split into teams of three, with each team designing a robot that can autonomously navigate an obstacle course and collect “food packages” represented by metal cylinders. The food packages are visually identical but vary in mass from 0.5 kg to 1 kg. Two robots are placed in the arena at the same time and after 5 minutes, or when all the food packages have been picked up, the robot with the most mass wins. Each team must face off each other in a round-robin style competition, at the end of which the team with the most victories is labelled the winner.
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

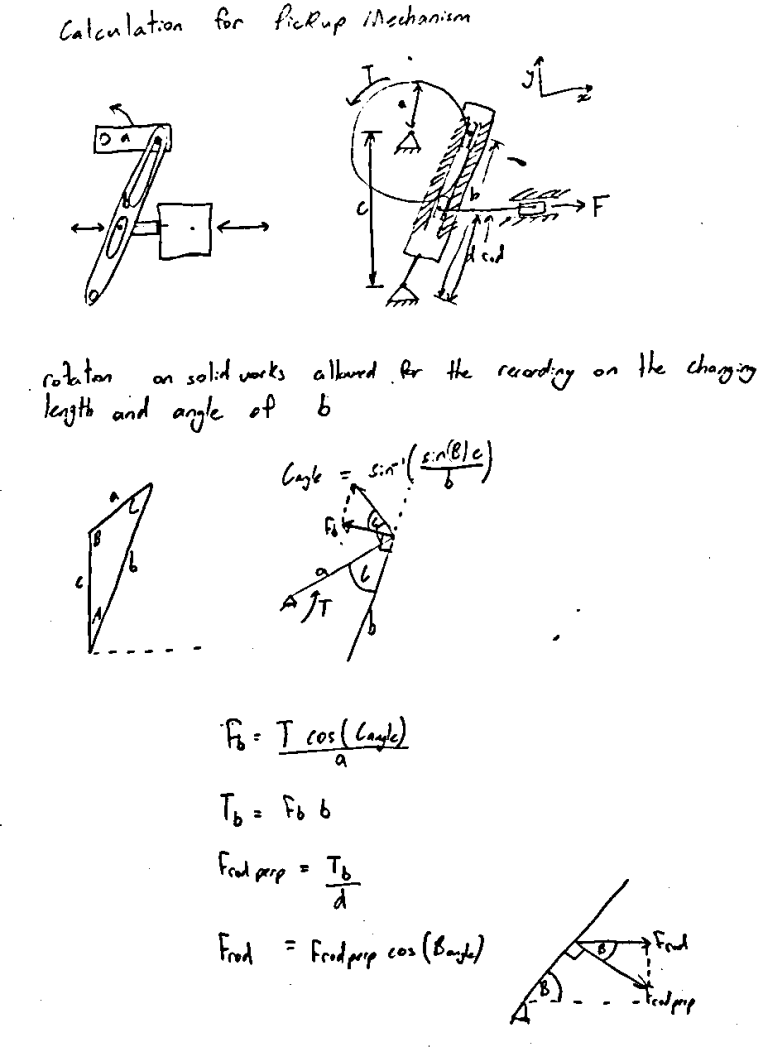
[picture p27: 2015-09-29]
Reports/Photos/Picture1.png

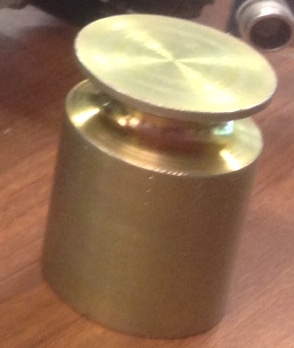
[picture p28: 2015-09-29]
Reports/Photos/IMG_0670 copy.JPG

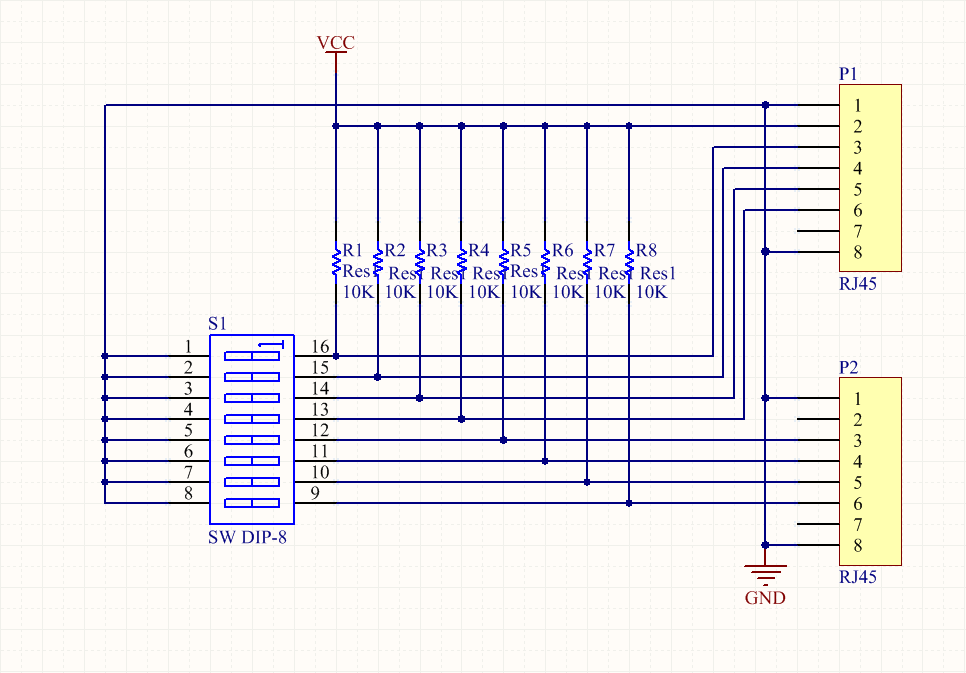
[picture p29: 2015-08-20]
Reports/Graphics/Circuit2 design.PNG

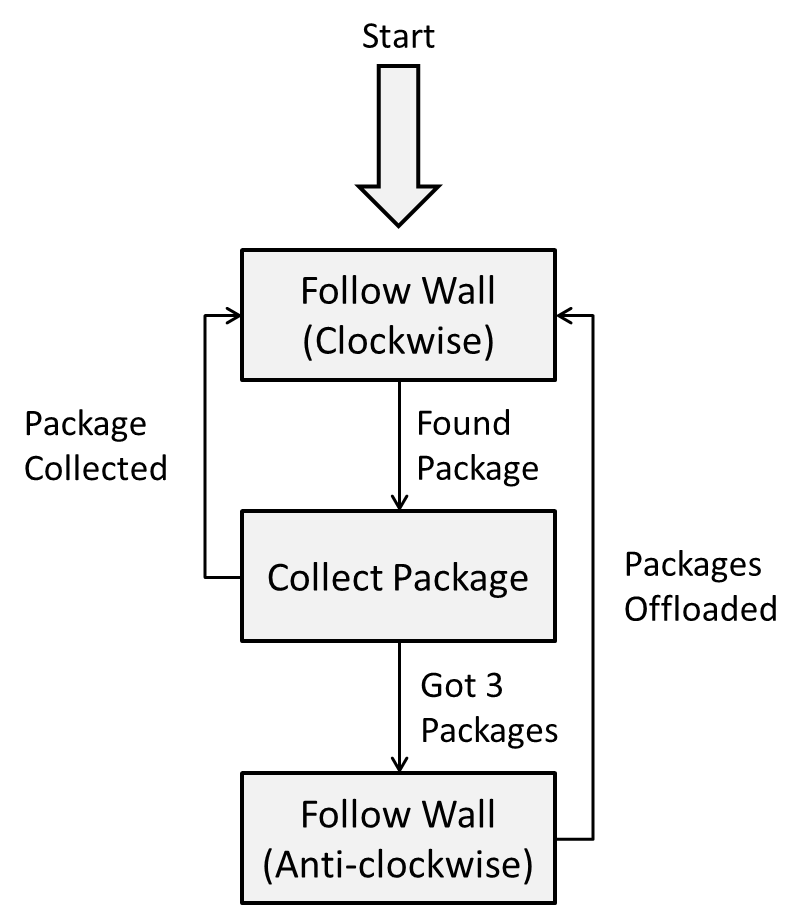
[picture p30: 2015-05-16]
Reports/Graphics/Tactic2.png

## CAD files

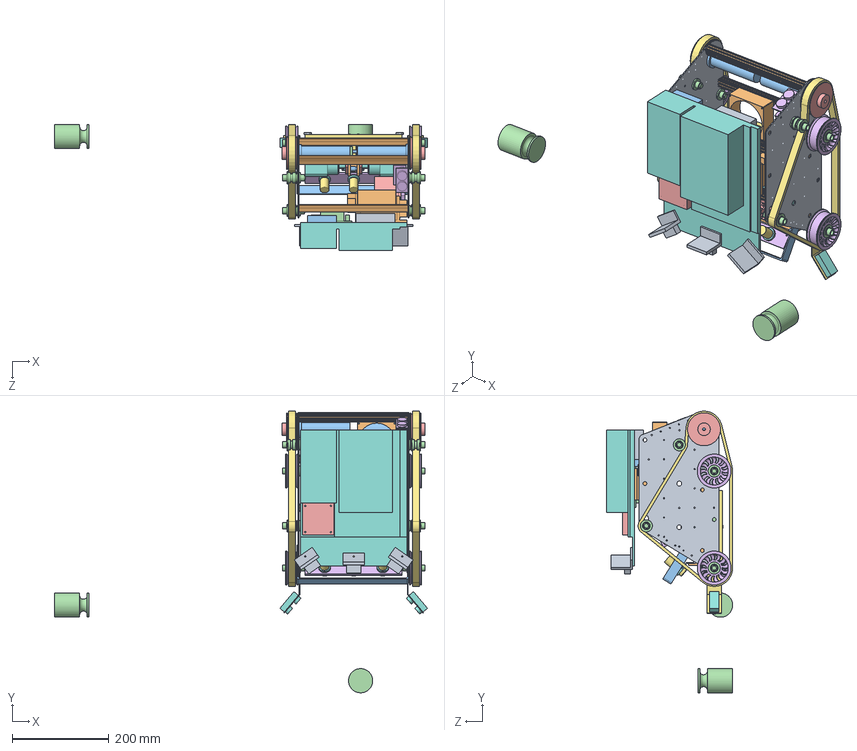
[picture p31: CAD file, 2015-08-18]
3D models/assemblies/cassie w motor.SLDASM
769.2 x 580.9 x 260.4 mm
Wall chassie x 2
Alloy extrustion x 4
Motor x 2
Track bearing x 8
Their wheel x 2
our wheel x 4
Belt1-2^cassie w motor x 2
Battery and ardunio
digital interface
power managment
sabertooth driver
stepper motor driver
servo interface
switches
geared stepper motor x 2
front
rod x 2
pin
drive gear bracket
cam x 2
magnet x 3
magnet bracket x 3
magnet arm x 6
rod fixtrue x 2
pickup fixture x 2
drive axel
magnet arm extrention
magnet arm extrention 2 x 2
sheild
weight sensor x 3
weight sensor nut x 6
bolt pick up x 2
sheild 2
sheild bracket x 2
weight x 2
ultrasonic mount x 2
ultrasonic x 2
IR sensor mid x 3
fan

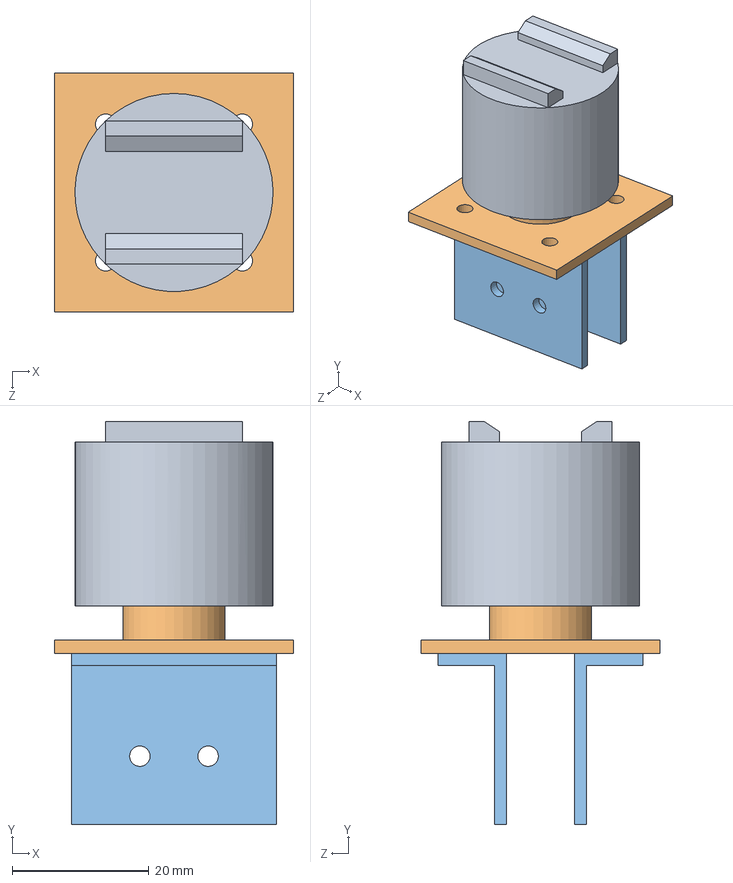
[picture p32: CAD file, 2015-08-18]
3D models/assemblies/magnet middle.SLDASM
35.0 x 59.0 x 35.0 mm
magnet
magnet bracket
magnet arm x 2

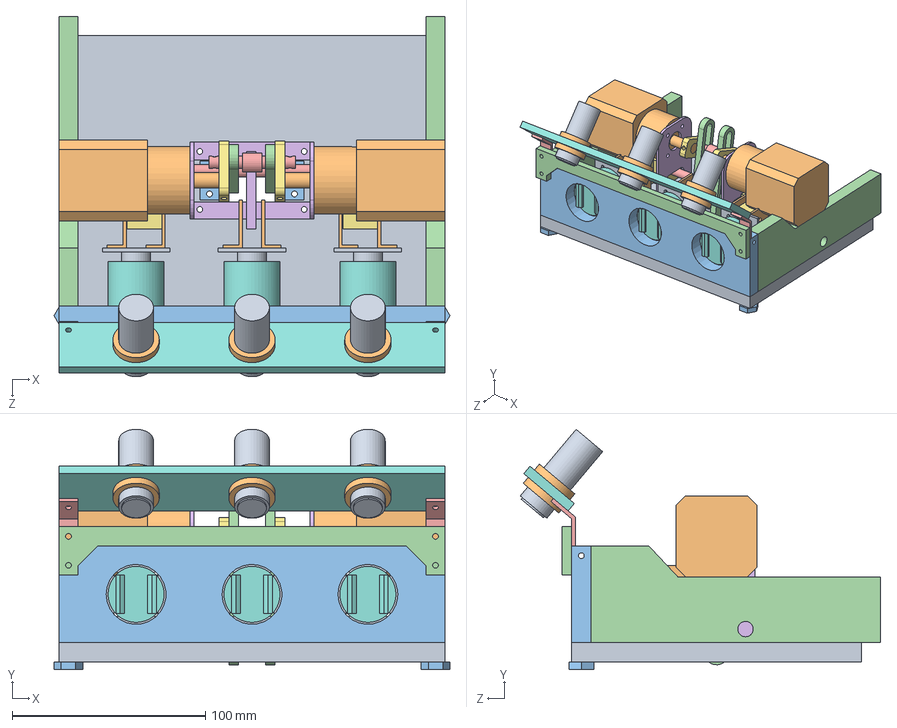
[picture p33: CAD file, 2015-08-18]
3D models/assemblies/pick up assem.SLDASM
205.0 x 124.4 x 186.6 mm
geared stepper motor x 2
front
rod x 2
pin
drive gear bracket
cam x 2
magnet x 3
magnet bracket x 3
magnet arm x 6
rod fixtrue x 2
pickup fixture x 2
drive axel
magnet arm extrention
magnet arm extrention 2 x 2
sheild
weight sensor x 3
weight sensor nut x 6
bolt pick up x 2
sheild 2
sheild bracket x 2

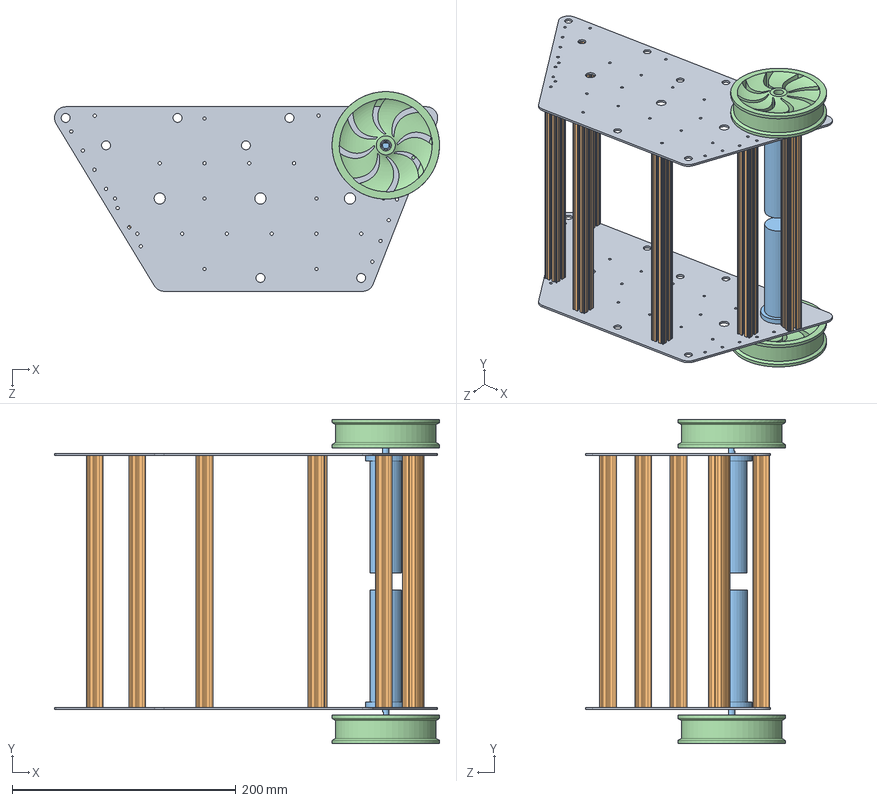
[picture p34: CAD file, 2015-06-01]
3D models/assemblies/track eletronics pickup.SLDASM
344.0 x 289.9 x 178.5 mm
Wall chassie x 2
Alloy extrustion x 7
Motor x 2
our wheel x 2

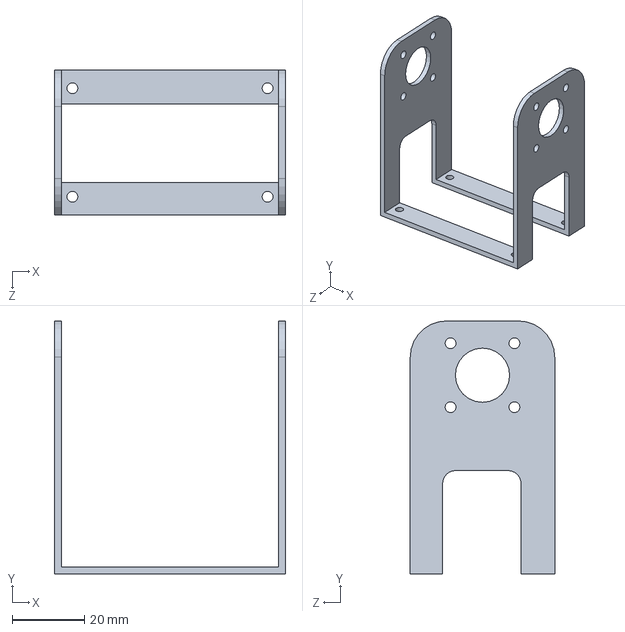
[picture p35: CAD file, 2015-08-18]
3D models/drive gear bracket.SLDPRT
64.0 x 70.0 x 40.0 mm

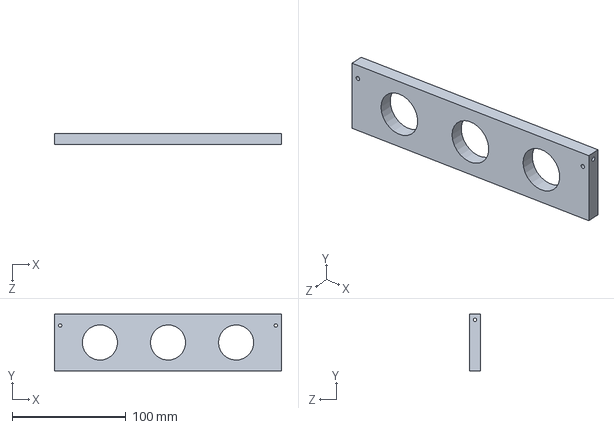
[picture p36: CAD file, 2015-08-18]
3D models/front.SLDPRT
200.0 x 50.0 x 10.0 mm

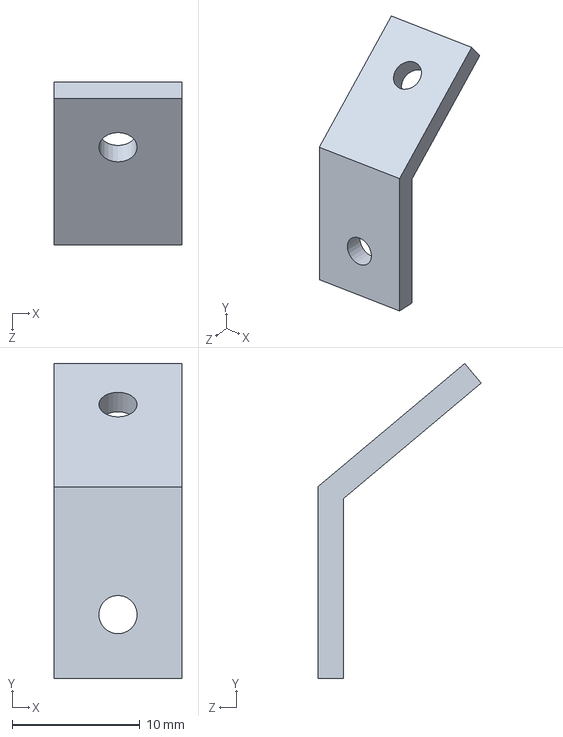
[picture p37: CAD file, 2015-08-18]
3D models/sheild bracket.SLDPRT
10.0 x 24.6 x 12.8 mm

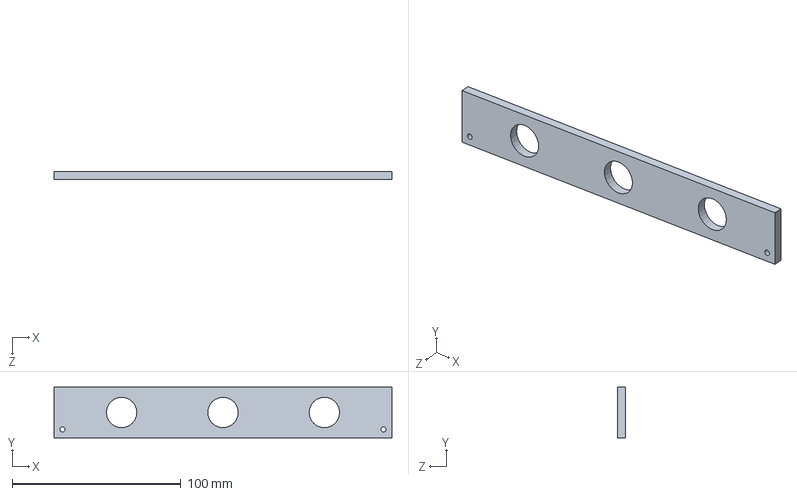
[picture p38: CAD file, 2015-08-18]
3D models/sheild.SLDPRT
200.0 x 30.0 x 5.00 mm

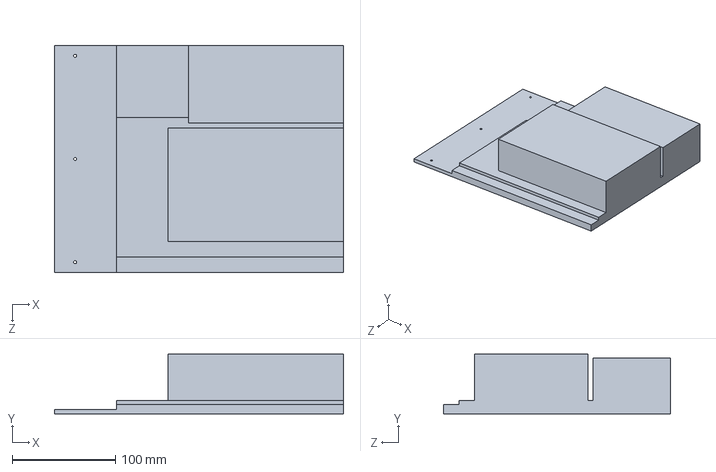
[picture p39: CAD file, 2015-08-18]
3D models/Battery and ardunio.SLDPRT
280.0 x 58.0 x 220.0 mm

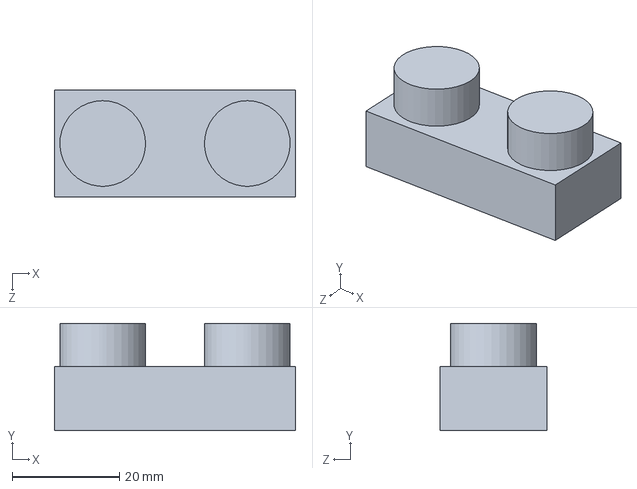
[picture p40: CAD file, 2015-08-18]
3D models/ultrasonic.SLDPRT
45.0 x 20.0 x 20.0 mm

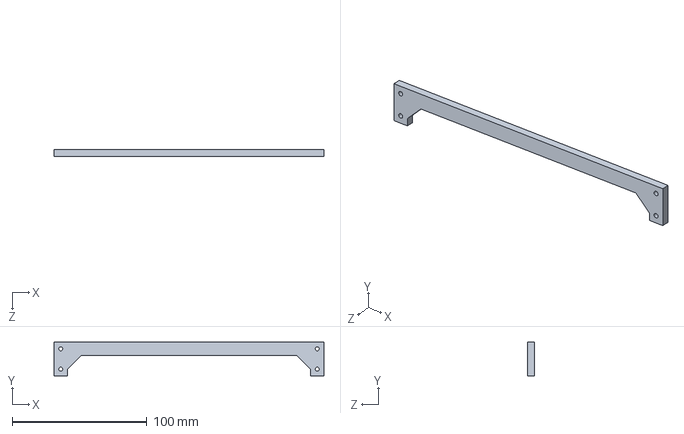
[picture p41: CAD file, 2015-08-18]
3D models/sheild 2.SLDPRT
200.0 x 25.0 x 5.00 mm

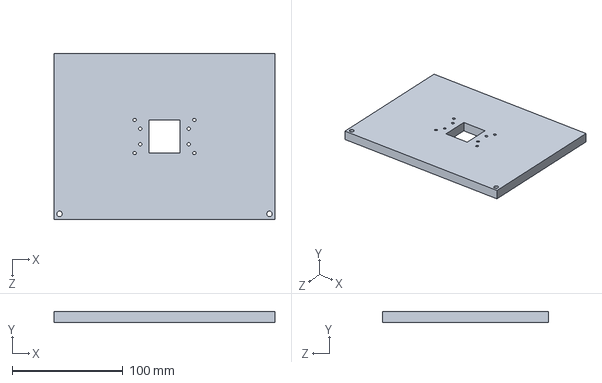
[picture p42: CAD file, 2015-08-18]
3D models/shell.SLDPRT
200.0 x 10.0 x 150.0 mm

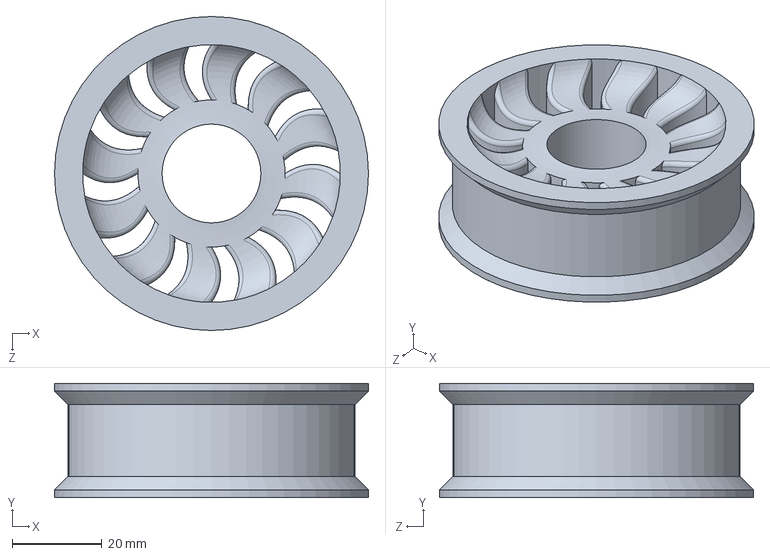
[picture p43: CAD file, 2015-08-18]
3D models/our wheel.SLDPRT
70.0 x 25.5 x 70.0 mm

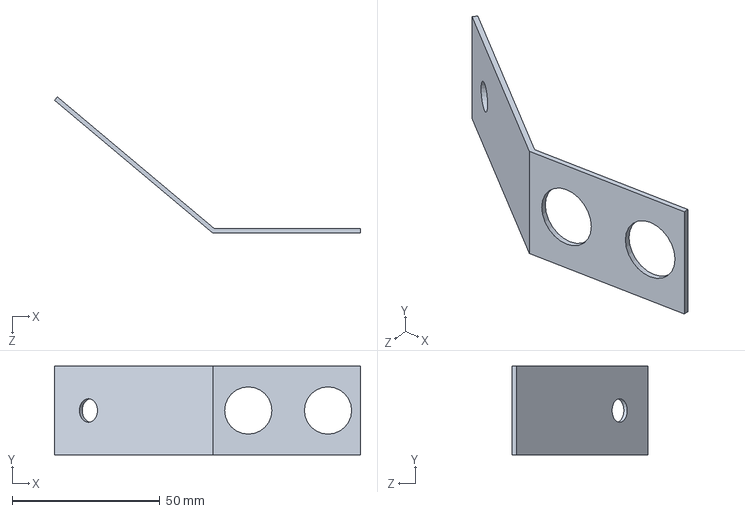
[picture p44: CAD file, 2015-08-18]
3D models/ultrasonic mount.SLDPRT
103.6 x 30.0 x 46.1 mm

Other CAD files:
3D models/assemblies/magnet.SLDASM
3D models/steel suport.SLDPRT
3D models/our wheel right.STL
3D models/magnet arm.SLDPRT
3D models/Alloy extrustion.SLDPRT
3D models/IR sensor mid.SLDPRT
3D models/M5 screw.SLDPRT
3D models/Motor.SLDPRT
3D models/Their wheel.SLDPRT
3D models/Track bearing.SLDPRT
3D models/Wall chassie.SLDPRT
3D models/assemblies/bolt pick up.SLDPRT
3D models/big servo.SLDPRT
3D models/cam.SLDPRT
3D models/digital interface.SLDPRT
3D models/drawings/3D printed wheel.SLDDRW
3D models/drawings/Perspex Parts.SLDDRW
3D models/drawings/Pickup Mechanism Parts.SLDDRW
3D models/drawings/Steel Pins.SLDDRW
3D models/drawings/Template.SLDDRW
3D models/drawings/cam.SLDDRW
3D models/drawings/cassie w motor sensor.SLDDRW
3D models/drawings/cassie w motor.SLDDRW
3D models/drawings/drive gear bracket.SLDDRW
3D models/drawings/magnet arm.SLDDRW
3D models/drawings/rod.SLDDRW
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

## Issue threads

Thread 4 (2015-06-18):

The Exception_t ADT has issues

petern3, 2015-06-18:
When trying to print (by serial) the exception, it seems to print the program memory. As soon as I don't dynamically allocate the memory it prints fine, but that's just wrong. To work around it, I'm simply not displaying any of them.

petern3, 2015-07-23:
I've changed the exceptions from structs to classes, as well as changing the strings to char* . Now it still doesn't print the exception, but now it prints nothing (with the newline) rather than the program memory. It one step better!

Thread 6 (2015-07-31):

HOT Board (and analog in not working)

petern3, 2015-07-31:
After doing no hardware changes, the analog ports stopped working , and the arduino power managing board got exceptionally hot (80 degrees+ ?). I suspect either:
 - a short somewhere, or
 - something to do with the analog reference voltage. I had previously changed it to INTERNAL2V56 and has worked, but it's a possible culprit.

petern3, 2015-08-03:
The Arduino itself had something wrong with it. Having been replaced, the sensors work fine

Closed 2015-08-03.

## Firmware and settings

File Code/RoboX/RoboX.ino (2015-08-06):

 ///////////////////////////////////////////////////////////////////////
/*----------------------------------------------------------------------
 * RoboX.ino
 *----------------------------------------------------------------------
 * 
 * Author:  Peter Nicholls
 * Created: 2015-05-26
 * Edited:  2015-06-18
 * 
 * This file is the main file, contatining the overall initialization
 * sequence and program kernel.
 * 
 *//////////////////////////////////////////////////////////////////////

///////////////
/// DEFINES ///
///////////////
#include "Arduino.h"
#include <inttypes.h>
#include <Servo.h>
#include <Herkulex.h>
#include <SPI.h>
#include <SD.h>
#include <TimerThree.h>
#include <Wire.h>
#include <Adafruit_TCS34725.h>

#include "config.h"
#include "actuator_core.h"
#include "audio_core.h"
#include "exception_core.h"
#include "interrupt_core.h"
#include "map_core.h"
#include "sensor_core.h"
#include "tactics_core.h"
#include "trig_core.h"

//////////////////////
/// INITIALIZATION ///
//////////////////////
void setup() {
  Serial.begin(BAUD_RATE);
  PRINTLN("\nInitializing:");
  
  init_actuator_core();
  init_audio_core();
  init_map_core();
  init_sensor_core();
  init_tactics_core();
  
  PRINTLN("Ready!\n");
  
  //display_map();
}

//////////////////////////////
/// MASTER CONTROL PROGRAM ///
//////////////////////////////
void loop() {
  switch (OPERATION_MODE) {
    case PRIMARY_MODE:
      primary_tactic();
      break;
    case SECONDARY_MODE:
      secondary_tactic();
      break;
    case MANUAL_MODE:
      manual_mode();
      break;
    default:
      idle_mode();
  }
}

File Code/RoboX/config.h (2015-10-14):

 ///////////////////////////////////////////////////////////////////////
/*----------------------------------------------------------------------
 * config.h
 *----------------------------------------------------------------------
 * 
 * Author:  Peter Nicholls
 * Created: 2015-05-26
 * Edited:  2015-06-18
 * 
 * Blurb
 * 
 *//////////////////////////////////////////////////////////////////////
 

#ifndef CONFIG_H
#define CONFIG_H

#include "Arduino.h"

//////////////
/// PINOUT ///
//////////////
// analogWrite() will not work on pins 9 and 10 due to TimerThree
// analogWrite() may not work on pins 11 and 3 due to Speaker
#define DC_LEFT_PIN 12
#define DC_RIGHT_PIN 13
#define DC_LEFT_INTERRUPT_PIN 5  // to check
#define DC_RIGHT_INTERRUPT_PIN 4

#define SERVO1_PIN 3
#define SERVO2_PIN 2

#define SMART_SERVO1_ADDRESS 0xFD

#define STEPPER1_STEP_PIN 42
#define STEPPER1_DIR_PIN 43
#define STEPPER2_STEP_PIN 44
#define STEPPER2_DIR_PIN 45

#define IR_SHT1_PIN A5 //10
//#define IR_SHT2_PIN A1 //11
#define IR_MED1_PIN A2
#define IR_MED2_PIN A3
#define IR_LNG1_PIN A4
#define IR_LNG2_PIN A0
#define USONIC3_TRIG_PIN 7
#define USONIC3_ECHO_PIN 6
#define USONIC2_TRIG_PIN 11
#define USONIC2_ECHO_PIN 10
#define USONIC1_TRIG_PIN 9
#define USONIC1_ECHO_PIN 8
#define SONAR1_PIN A6

#define IR_VAR1_PIN 26 // 30  // left
#define IR_VAR2_PIN 28 // 32  // middle
#define IR_VAR3_PIN 30 // 34  // right
#define LIMIT_O_PIN 32 // 36
#define TURN_ON_PIN A9

#define CHIP_SELECT_PIN 53
#define SPEAKER_PIN 5
#define SPEAKER_ENABLE_PIN A10

#define DIP8_S1_PIN 38 // WORKS - PRIMARY/MANUAL
#define DIP8_S2_PIN 39 // DOESNT
#define DIP8_S3_PIN 40 // WORKS - WEIGHT_CHASING_ENABLE
#define DIP8_S4_PIN 41 // WORKS - MAGNET_EXTEND_ENABLE
#define DIP8_S5_PIN 34 // WORKS - MAGNET_RAISE_ENABLE
#define DIP8_S6_PIN 35 // DOESNT
#define DIP8_S7_PIN 36 // WORKS - MOTOR_ENABLE
#define DIP8_S8_PIN 37 // DOESNT


////////////////////////
/// SCHEDULER CONFIG ///
////////////////////////
//#define TIMERTHREE_PERIOD 1000  // microseconds
#define PRIMARY_TACTIC_PERIOD 1000000  // microseconds  // 1Hz
#define SECONDARY_TACTIC_PERIOD 50000  // microseconds  // 20Hz
#define MANUAL_CONTROL_PERIOD 100000  // microseconds   // 10Hz

#define IDLE_TIMEOUT 10000  // milliseconds

///////////////////////////
/// USER CONTROL CONFIG ///
///////////////////////////
#define FORWARD_INCREMENT 10
#define TURNING_INCREMENT 10

#define FWD 'w'
#define BWD 's'
#define LFT 'a'
#define RHT 'd'
#define STP 'x'
#define EXTEND 'h'
#define RETRACT 'g'
#define TOGGLE 't'
#define RAISE 'r'
#define LOWER 'f'

///////////////////////
/// ACTUATOR CONFIG ///
///////////////////////
/// DC MOTOR CONFIG ///
#define ENCODER_PPR 330  // 663
#define ENCODER_RESET_TIMEOUT 10000 // microseconds
#define DC_FORWARD true
#define DC_BACKWARD false
#define AUTO_CALIBRATE_DC
#define DC_CALIBRATION_LIMIT 15 // 90 +/- n

#define SPEED_P 0.2
#define ROTATE_P 0.35
#define ANGLE_LIMIT 45

/// STEPPER MOTOR CONFIG ///
#define STEPPER1_SPR 1036 // 630/1.8*5.18 Geared
#define STEPPER2_SPR 1036 // Geared
//#define STEPPER3_SPR 200  // to calibrate
//#define STEPPER4_SPR 200  // to calibrate

/// SERVO CONFIG ///
#define MAX_TRAVEL 100

/*
  LED_GREEN
  LED_BLUE
  LED_CYAN
  LED_RED
  LED_GREEN2
  LED_PINK
  LED_WHITE
*/

/////////////////////
/// SENSOR CONFIG ///
/////////////////////
// USONIC 1 is left
// USONIC 2 is right
// USONIC 3 is upper centre
// IR_MED1 left one
// IR_MED2 right one
#define IR_SHT1_OFFSET {-80, -80}
#define IR_SHT1_ANGLE -90
#define IR_MED1_OFFSET {-100, 100}
#define IR_MED1_ANGLE 35
#define IR_MED2_OFFSET {100, 100}
#define IR_MED2_ANGLE -35
#define IR_LNG1_OFFSET {0, 60}
#define IR_LNG1_ANGLE 0
#define IR_LNG2_OFFSET {0, 0}
#define IR_LNG2_ANGLE 0
#define USONIC1_OFFSET {135, -150}
#define USONIC1_ANGLE 50
#define USONIC2_OFFSET {-135, -150}
#define USONIC2_ANGLE -50
#define USONIC3_OFFSET {0, 50}
#define USONIC3_ANGLE 0
#define SONAR1_OFFSET {0, 50}
#define SONAR1_ANGLE 0


#define IR_SHT_MIN_ADC 970   // To measure
#define IR_SHT_DV1_ADC 360   // to measure
#define IR_SHT_DV2_ADC 220   // to measure
#define IR_SHT_MAX_ADC 150  // To measure
#define IR_SHT_MIN_MM 40
#define IR_SHT_DV1_MM 120
#define IR_SHT_DV2_MM 200
#define IR_SHT_MAX_MM 300

#define IR_MED_MIN_ADC 976   // To measure
#define IR_MED_DV1_ADC 380   // to measure
#define IR_MED_DV2_ADC 237   // to measure
#define IR_MED_MAX_ADC 164  // To measure
#define IR_MED_MIN_MM 100
#define IR_MED_DV1_MM 300
#define IR_MED_DV2_MM 500
#define IR_MED_MAX_MM 800

#define IR_LNG_MIN_ADC 930   // To measure
#define IR_LNG_DV1_ADC 575   // to measure
#define IR_LNG_DV2_ADC 375   // to measure 
#define IR_LNG_MAX_ADC 240  // To measure
#define IR_LNG_MIN_MM 200
#define IR_LNG_DV1_MM 400
#define IR_LNG_DV2_MM 600
#define IR_LNG_MAX_MM 1000
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

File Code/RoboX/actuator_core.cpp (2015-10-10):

 ///////////////////////////////////////////////////////////////////////
/*----------------------------------------------------------------------
 * actuator_core.cpp
 *----------------------------------------------------------------------
 * 
 * Author:  Peter Nicholls
 * Created: 2015-05-31
 * Edited:  2015-06-18
 * 
 * Blurb
 * 
 *//////////////////////////////////////////////////////////////////////


#include "actuator_core.h";
#include "exception_core.h"
#include "interrupt_core.h"
#include "trig_core.h"

///////////////
/// GLOBALS ///
///////////////
DCMotor DC;

ServoMotor SERVO1;
ServoMotor SERVO2;

StepperMotor STEPPER1;
StepperMotor STEPPER2;

uint8_t SERVO_COLOUR = LED_WHITE;


/////////////////
/// FUNCTIONS ///
/////////////////
void init_actuator_core(void) {
  PRINT("\tDC Motors...");
  
  // DC Motors
  DC.initialize();
  
  attachInterrupt(DC_LEFT_INTERRUPT_PIN, left_encoder_ISR, RISING);  // can do 'CHANGE', but would include twice the interrupts (high CPU load)
  attachInterrupt(DC_RIGHT_INTERRUPT_PIN, right_encoder_ISR, RISING);

  #ifdef AUTO_CALIBRATE_DC
    DC.calibrate();
  #endif
  
  if (DC_MOTOR_ERROR.is_active) {
    PRINTLN("failed");
  }
  else {
    PRINT("zero set to ");
    PRINTLN(DC.zero);
  }
  
  PRINT("\tActuators...");
  // Servos
  SERVO1.initialize(SERVO1_PIN);
  SERVO2.initialize(SERVO2_PIN);
  
  // Stepper Motors
  STEPPER1.initialize(STEPPER1_STEP_PIN, STEPPER1_DIR_PIN, STEPPER1_SPR);
  STEPPER2.initialize(STEPPER2_STEP_PIN, STEPPER2_DIR_PIN, STEPPER2_SPR);
  
  // Smart Servos
  Herkulex.beginSerial2(115200);  // When in port C2 for Transmit/Receive #2
  Herkulex.reboot(SMART_SERVO1_ADDRESS);
  delay(500);
  Herkulex.initialize();
  //delay(200);
  Herkulex.moveOneAngle(SMART_SERVO1_ADDRESS, 0, 200, SERVO_COLOUR);
  
  PRINTLN("done");
}


////////////////////////////////
/// DC MOTOR CLASS FUNCTIONS ///
////////////////////////////////
void DCMotor::initialize(void) {
  this->zero = 90;
  this->left_motor.attach(DC_LEFT_PIN);
  this->right_motor.attach(DC_RIGHT_PIN);
}

void DCMotor::calibrate(void) {
  this->left_motor.write(this->zero);
  this->right_motor.write(this->zero);
  uint8_t dc_high_limit = this->zero;
  uint8_t dc_low_limit = this->zero;
  
  // get the point at which the motor moves forward
  while (LEFT_ROTATION == 0.0 || RIGHT_ROTATION == 0.0) {
    this->left_motor.write(dc_high_limit);
    this->right_motor.write(dc_high_limit);
    if (dc_high_limit > (this->zero + DC_CALIBRATION_LIMIT)) {
      DC_MOTOR_ERROR.activate();
      //DC_MOTOR_ERROR.report();
      break;
    }
    dc_high_limit++;
    delay(100);
  }
  
  // reset the conditions
  this->left_motor.write(this->zero);
  this->right_motor.write(this->zero);
  delay(500);
  LEFT_ROTATION = 0.0;
  RIGHT_ROTATION = 0.0;
  
  // get the point at which the motors move backward
  while (LEFT_ROTATION == 0.0 || RIGHT_ROTATION == 0.0) {
    this->left_motor.write(dc_low_limit);
    this->right_motor.write(dc_low_limit);
    if (dc_low_limit < (this->zero - DC_CALIBRATION_LIMIT)) {
      DC_MOTOR_ERROR.activate();
      //DC_MOTOR_ERROR.report();
      break;
    }
    dc_low_limit--;
    delay(100);
  }
  
  this->zero = (dc_high_limit + dc_low_limit) / 2;
  this->left_motor.write(this->zero);
  this->right_motor.write(this->zero);
}

void DCMotor::drive(int16_t motor_speed, int16_t motor_rotation) {
  // 
  
  if (motor_speed > 90) {
    motor_speed = 90;
  }
  else if (motor_speed < -90) {
    motor_speed = -90;
  }
  if (motor_rotation > 90) {
    motor_rotation = 90;
  }
  else if (motor_rotation < -90) {
    motor_rotation = -90;
  }
  
  int16_t left_drive = this->zero - (motor_speed + motor_rotation);  // subtract motor speed due to upside-down chassis
  int16_t right_drive = this->zero - (motor_speed - motor_rotation);
 
  if (left_drive < 0) {
    left_drive = 0;
    right_drive = 2*motor_rotation;
  }
  else if (left_drive > 180) {
    left_drive = 180;
    right_drive = 180 - (2*motor_rotation);
  }

  else if (right_drive < 0) {
    right_drive = 0;
    left_drive = 2*motor_rotation;
  }
  else if (right_drive > 180) {
    right_drive = 180;
    left_drive = 180 - (2*motor_rotation);
  }
  
  if (left_drive > 90) {
    LEFT_DIR = DC_FORWARD;
  } else {
    LEFT_DIR = DC_BACKWARD;
  }
  if (right_drive > 90) {
    RIGHT_DIR = DC_FORWARD;
  } else {
    RIGHT_DIR = DC_BACKWARD;
  }
  
  this->left_motor.write(left_drive);
  this->right_motor.write(right_drive);
  
}

///////////////////////////////////
/// SERVO MOTOR CLASS FUNCTIONS ///
///////////////////////////////////
void ServoMotor::initialize(uint8_t init_port) {
  this->servo.attach(init_port);
}

void ServoMotor::rotate(int16_t servo_position) {
  this->servo.write(servo_position);
}

/////////////////////////////////////
/// STEPPER MOTOR CLASS FUNCTIONS ///
/////////////////////////////////////
void StepperMotor::initialize(uint8_t init_step_pin, uint8_t init_dir_pin, int16_t init_steps_per_rev) {
  this->step_pin = init_step_pin;
  this->dir_pin = init_dir_pin;
  this->steps_per_rev = init_steps_per_rev;
  pinMode(init_step_pin, OUTPUT);
  pinMode(init_dir_pin, OUTPUT);
}

void StepperMotor::rotate(int16_t num_degrees) {
  uint32_t steps_left = abs(((int32_t)num_degrees * this->steps_per_rev) / 360);
  
  if (num_degrees > 0) {
    digitalWrite(this->dir_pin,LOW);
  } else {
    digitalWrite(this->dir_pin,HIGH);
  }
  
  for (steps_left; steps_left > 0; steps_left--) {
    digitalWrite(this->step_pin, LOW);
    delayMicroseconds(2);
    digitalWrite(this->step_pin, HIGH);
    delay(1);
  }
}

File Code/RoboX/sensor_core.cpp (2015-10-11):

 ///////////////////////////////////////////////////////////////////////
/*----------------------------------------------------------------------
 * sensor_core.cpp
 *----------------------------------------------------------------------
 * 
 * Author:  Peter Nicholls
 * Created: 2015-05-31
 * Edited:  2015-05-31
 * 
 * Blurb
 * 
 *//////////////////////////////////////////////////////////////////////
 
////////////////
/// INCLUDES ///
////////////////
#include "sensor_core.h"
#include "exception_core.h"

///////////////
/// GLOBALS ///
///////////////
InfraredSensor IR_SHT1;
InfraredSensor IR_MED1;
InfraredSensor IR_MED2;
InfraredSensor IR_LNG1;
InfraredSensor IR_LNG2;
UltrasonicSensor USONIC1;
UltrasonicSensor USONIC2;
UltrasonicSensor USONIC3;
SonarSensor SONAR1;

DigitalSensor IR_VAR1;
DigitalSensor IR_VAR2;
DigitalSensor IR_VAR3;
DigitalSensor LIMIT_O;
DigitalSensor TURN_ON;

DigitalSensor DIP8_S1;
DigitalSensor DIP8_S2;
DigitalSensor DIP8_S3;
DigitalSensor DIP8_S4;
DigitalSensor DIP8_S5;
DigitalSensor DIP8_S6;
DigitalSensor DIP8_S7;
DigitalSensor DIP8_S8;

IMUSensor IMU;
ColourSensor COLOUR;


//uint32_t USONIC_TIMEOUT_VALUE = USONIC_TIMEOUT;

/////////////////
/// FUNCTIONS ///
/////////////////
static void I2Cread(uint8_t Address, uint8_t Register, uint8_t Nbytes, uint8_t* Data) {
  // This function read Nbytes bytes from I2C device at address Address. 
  // Put read bytes starting at register Register in the Data array. 

  // Set register address
  Wire.beginTransmission(Address);
  Wire.write(Register);
  Wire.endTransmission();
 
  // Read Nbytes
  Wire.requestFrom(Address, Nbytes); 
  uint8_t index=0;
  while (Wire.available()) {
    Data[index++]=Wire.read();
  }
}
 
static void I2CwriteByte(uint8_t Address, uint8_t Register, uint8_t Data) {
  // Write a byte (Data) in device (Address) at register (Register)
  
  // Set register address
  Wire.beginTransmission(Address);
  Wire.write(Register);
  Wire.write(Data);
  Wire.endTransmission();
}

void init_sensor_core(void) {
  PRINT("\tSensors...");
  analogReference(INTERNAL2V56);
  Wire.begin();

  int8_t IR_SHT1_OFFSET_TEMP[2] = IR_SHT1_OFFSET;
  int8_t IR_MED1_OFFSET_TEMP[2] = IR_MED1_OFFSET;
  int8_t IR_MED2_OFFSET_TEMP[2] = IR_MED2_OFFSET;
  int8_t IR_LNG1_OFFSET_TEMP[2] = IR_LNG1_OFFSET;
  int8_t IR_LNG2_OFFSET_TEMP[2] = IR_LNG2_OFFSET;
  int8_t USONIC1_OFFSET_TEMP[2] = USONIC1_OFFSET;
  int8_t USONIC2_OFFSET_TEMP[2] = USONIC2_OFFSET;
  int8_t USONIC3_OFFSET_TEMP[2] = USONIC3_OFFSET;
  int8_t SONAR1_OFFSET_TEMP[2] = SONAR1_OFFSET;

  IR_SHT1.initialize(IR_SHT1_PIN, SHT_RANGE, IR_SHT1_OFFSET_TEMP, degrees_to_radians(IR_SHT1_ANGLE));
  IR_MED1.initialize(IR_MED1_PIN, MED_RANGE, IR_MED1_OFFSET_TEMP, degrees_to_radians(IR_MED1_ANGLE));
  IR_MED2.initialize(IR_MED2_PIN, MED_RANGE, IR_MED2_OFFSET_TEMP, degrees_to_radians(IR_MED2_ANGLE));
  IR_LNG1.initialize(IR_LNG1_PIN, LNG_RANGE, IR_LNG1_OFFSET_TEMP, degrees_to_radians(IR_LNG1_ANGLE));
  IR_LNG2.initialize(IR_LNG2_PIN, LNG_RANGE, IR_LNG2_OFFSET_TEMP, degrees_to_radians(IR_LNG2_ANGLE));
  USONIC1.initialize(USONIC1_TRIG_PIN, USONIC1_ECHO_PIN, USONIC1_OFFSET_TEMP, degrees_to_radians(USONIC1_ANGLE));
  USONIC2.initialize(USONIC2_TRIG_PIN, USONIC2_ECHO_PIN, USONIC2_OFFSET_TEMP, degrees_to_radians(USONIC2_ANGLE));
  USONIC3.initialize(USONIC3_TRIG_PIN, USONIC3_ECHO_PIN, USONIC3_OFFSET_TEMP, degrees_to_radians(USONIC3_ANGLE));
  SONAR1.initialize(SONAR1_PIN, SONAR1_OFFSET_TEMP, degrees_to_radians(SONAR1_ANGLE));
  
  IR_VAR1.initialize(IR_VAR1_PIN, LOW, INPUT);
  IR_VAR2.initialize(IR_VAR2_PIN, LOW, INPUT);
  IR_VAR3.initialize(IR_VAR3_PIN, LOW, INPUT);
  LIMIT_O.initialize(LIMIT_O_PIN, HIGH, INPUT_PULLUP);
  TURN_ON.initialize(TURN_ON_PIN, HIGH, INPUT_PULLUP);
  
  DIP8_S1.initialize(DIP8_S1_PIN, LOW, INPUT_PULLUP);
  DIP8_S2.initialize(DIP8_S2_PIN, LOW, INPUT_PULLUP);
  DIP8_S3.initialize(DIP8_S3_PIN, LOW, INPUT_PULLUP);
  DIP8_S4.initialize(DIP8_S4_PIN, LOW, INPUT_PULLUP);
  DIP8_S5.initialize(DIP8_S5_PIN, LOW, INPUT_PULLUP);
  DIP8_S6.initialize(DIP8_S6_PIN, LOW, INPUT_PULLUP);
  DIP8_S7.initialize(DIP8_S7_PIN, LOW, INPUT_PULLUP);
  DIP8_S8.initialize(DIP8_S8_PIN, LOW, INPUT_PULLUP);
  
  IMU.initialize();
  COLOUR.initialize();
  
  PRINTLN("done");
}

void update_sensors(void) {
  IR_SHT1.update();
  IR_MED1.update();
  IR_MED2.update();
  IR_LNG1.update();
  //IR_LNG2.update();
  
  USONIC1.update();
  USONIC2.update();
  USONIC3.update();
  
  //SONAR1.update();
}


void buffer_initialize(CircBuf_t* buffer, uint8_t size) {
  buffer->windex = 0;
  buffer->rindex = 0;
  buffer->size = size;
  buffer->data = (uint32_t *) calloc (size, sizeof(uint32_t));
  // Note use of calloc() to clear contents.
}

void buffer_store(CircBuf_t* buffer, uint32_t to_store){
  buffer->data[buffer->windex] = to_store;
  buffer->windex++;
  if (buffer->windex >= buffer->size) {
    buffer->windex = 0;
  }
}

uint32_t buffer_average(CircBuf_t buffer) {
  uint32_t sum = 0;
  for (uint8_t i=0; i < buffer.size; i++) {
    sum += buffer.data[i];
  }
  return sum / buffer.size;
}

uint32_t buffer_average_non_zero(CircBuf_t buffer) {
  uint32_t sum = 0;
  bool is_zero = false;
  for (uint8_t i=0; i < buffer.size; i++) {
    if (buffer.data[i]) {
      is_zero = true;
    }
    sum += buffer.data[i];
  }
  if (is_zero) {
    return 0;
  } else {
    return sum / buffer.size;
  }
}


///////////////////////////////////////
/// INFRARED SENSOR CLASS FUNCTIONS ///
///////////////////////////////////////
void InfraredSensor::initialize(uint8_t init_pin, uint8_t init_type, int8_t init_offset[2], float init_angle) {
  this->pin = init_pin;
  this->type = init_type;
  this->offset = init_offset;
  this->polar_value.theta = init_angle;
  buffer_initialize(&this->raw_value, SENSOR_BUFFER_SIZE);
}

void InfraredSensor::update(void) {
  /*int32_t sum = 0;
  for (uint8_t i=0; i < SENSOR_BUFFER_SIZE; i++) {
    sum += analogRead(this->pin);
  }
  this->raw_value = sum / SENSOR_BUFFER_SIZE;*/
  buffer_store(&this->raw_value, analogRead(this->pin));
  this->polar_value.r = NOT_READ;
  this->cart_value.x = NOT_READ;
}

PolarVec InfraredSensor::polar_read(void) {
  if (this->polar_value.r == NOT_READ) {  // Only converts value once
    if (this->type == SHT_RANGE) {
      this->read_sht();
    }
    else if (this->type == MED_RANGE) {
      this->read_med();
    }
    else if (this->type == LNG_RANGE) {
      this->read_lng();
    }
  }
  return this->polar_value;
}

CartVec InfraredSensor::cart_read(void) {
  if (this->cart_value.x == NOT_READ) {  // Only converts value once
    if (polar_read().r == NOT_VALID) {
      this->cart_value.x = NOT_VALID;
      this->cart_value.y = NOT_VALID;
    } 
    else {
      this->cart_value = this->polar_value + this->offset;
    }
  }
  return this->cart_value;
}
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

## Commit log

2015-05-05 - Inserted basic structure of report
2015-05-16 - Finished Tactics section - Added behavioural flowcharts
2015-05-16 - Move files, added reference material for me to read
2015-05-20 - Added Jack's N2 graph (not to the report though) - Added Merit table excel file
    [Merit Table.xlsx]
2015-05-22 The report is finally done!
    - Added section ondataflow diagram
    - Added more nfo in experiment
    - Updated and inserted figures
    - Cost comparisons
    - Formatting
    - PAGE NUMBERS!!
2015-05-25 3D models! enjoy
    [Alloy extrustion.SLDPRT, Battery and ardunio.SLDPRT, Motor.SLDPRT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]
2015-05-25 3d models
    [Wall chassie.SLDPRT, geared stepper motor.SLDPRT, magnet.SLDPRT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]
2015-06-02 Added documentation for the interface PCBs and added DC motor code
2015-06-09 It Compiles!!!! Added IR and Sonar API
    Still need to edit mapping
2015-06-09 THE CODE NOW UPLOADS AND DOES STUFF!!!!
    It was an issue with the exception core's exceptional callocing.
    [RoboX.ino, actuator_core.cpp, config.h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]
2015-06-11 Added Stepper motor code.
    This will probably give issues in scheduling later on. Potentially need to
    make it a PWM output, which can be done on these pins:
    - 2-13
    - 44-46
    [RoboX.ino, actuator_core.cpp, config.h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]
2015-06-11 Added variable IR code
    Can now easily create other boolean sensors as well.
    Still need to calibrate IR sensors, and write code for ultrasonic and
    sonar.
2015-06-16 Begun SD code
    Unfortunately came across large issues with the exception core.
    [RoboX.ino, actuator_core.cpp, config.h]
2015-06-18 Added interrupts for DC motor encoder
    It has not been tested yet.
2015-06-18 Adjusted datasheets and added a port printout
    Now we shouldn't need to refer to the documentation for plugging things
    in!
2015-07-01 Begun tactics
    Made some very simple serial commands
    Adjusted scheduling and operation modes
    Created sensor reading interrupt
    Finished code to delete old maps.
    None of this has been tested
2015-07-02 Fixed map removal code and (current) manual control
    Also added a simple test program to make the robot move using serial
    commands (test_code.ino)
    The main code DID NOT COMPILE on my machine (see the relevant issue for
    more info)
    [actuator_core.cpp, config.h, tactics_core.cpp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]
2015-07-13 Began adding I2C and IMU code
2015-07-13 Added current 3D models (Ryans)
    [Alloy extrustion.SLDPRT, Battery and ardunio.SLDPRT, M5 screw.SLDPRT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]
2015-07-17 Many more good changes
    - Added datasheets
    - Fixed encoder code
    - Fixed internal interrupts
    - Simplified sensor code for use in interrupts (need to calibrate later)
    - Added DC motor self-calibrating routine
    Still no luck with the IMU or speaker though.
    [RoboX.ino, actuator_core.cpp, config.h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]
2015-07-20 Converted sensors from structs to classes
    The program acts identically, and things should be easier to use.
    Also fixed spelling errors in the documentation file names
    [config.h, interrupt_core.cpp, sensor_core.cpp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]
2015-07-20 Added Ultrasonic code
2015-07-20 Converted actuators into classes
    Again, the code acts the same. Also discovered the ultrasonic sensors take
    a huge amount of time, unless something fancy is done. They'll be left out
    for now
2015-07-21 Got the pick-up mechanism moving!
    - Added code to make two motors move in sync
    - Tidied up exception core code
    - Added (not functional) Colourview code
    - Made sections more distinguishable
2015-07-27 Continued work on Secondary Tactic
    - Some support trig conversion functions written
    - Added ability to change between tactics during run-time
    - Also tested Herkulex servos. Only has position control from -150 to 150
2015-07-30 Converted polar and cartesian vectors to classes
    - Changed sensor outputs to vectors
    - This includes:
    polar relative to the sensor
    cartesian, relative to the robot centre
    - Added weight detection function
    - Added basic secondary tactic loop
2015-08-03 Beginning to add audio code
    instead of trying to run .wav files, it will be much easier to
    use rtttl files (ringtones). It doesn't really work yet.
    [RoboX.ino, actuator_core.cpp, audio_core.cpp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]
2015-08-03 solidworks updates
    [Battery and ardunio.SLDPRT, IR sensor mid.SLDPRT, Wall chassie.SLDPRT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]
2015-08-05 Basic Wall following implemented
    - Finally chases weights! (could be improved)
    - Finally avoids obsticals! (also could be improved)
    - Doesn't do both at the same time very well though.
    - Added circular buffer code and implemented in IR sensors
    [actuator_core.cpp, config.h, sensor_core.cpp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]
2015-08-06 Added special features
    - The smart servo now points
    - The speaker now plays rtttl files
    - Attempted to improve navigation. It doesn't see weights in the right
    place.
    [actuator_core.cpp, audio_core.cpp, config.h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]
2015-08-06 Added a zip of the dependencies (libraries)
    - Minor changes to tactics
    - Added sonar class
2015-08-06 Changed some print lines
2015-08-20 Circuit board
    [PCB1.PcbDoc, PCB_Project.PrjPcb, Sheet1.SchDoc]
2015-08-23 More report proofreading
    - Proofread whole report
    - Finished all my sections
    The only things that could be changed now are:
    - A pic of our robot for the front cover (or something)
    - Changing the pics of the sensors to face the correct way
    - Finishing the BOM(particularly circuit 3). If the 'additional materials'
    section is changed, so does the relevent specification
    Note: Be VERY careful about reformatting to change pages. Changing the
    contents page is a pain. IF you do need to change it:
    - Refresh entire table
    - Highligh it all, and remove spacing after paragraph
    - Refresh just page numbers
    - Fix the stupid appendix numbers manually
2015-08-24 Update for photos
    [3D printed wheel.SLDDRW, Perspex Parts.SLDDRW, Pickup Mechanism Parts.SLDDRW]
2015-09-07 Finally got colour sensor reading!
    It was taken out of the foreground tasks, and it read! It hasn't been
    calibrated yet. The IMU might be fixed by the same method
    [sensor_core.cpp, tactics_core.cpp]
2015-09-13 Got the Colour sensor and IMU going!
    Note that they have not been calibrated and the magnetometer still doesn't
    work. I'll leave the magnetometer for now because of the magnets.
    The secondary tactic does not work in this commit, as it is undergoing
    some major changes.
    [IMU_TEST.ino, Timekeeping.ino, actuator_core.cpp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]
2015-09-20 Continued work of secondary tactic
    Got the pointer servo working again, and part way to fixing the weight
    detection. Now also detects when weights are on-board happily.
    Also added a powerpoint file for presentations.
    [config.h, sensor_core.cpp, sensor_core.h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]
2015-09-24 Power point
2015-10-02 Major changes to secondary tactic
    - Moved Ryan's presentation
    - Added support to move backwards
    - Implemented rest of overall state machine. Still have to calibrate:
    - Colour sensor detection tolerances
    - Weight detection timeout
    [config.h, tactics_core.cpp]
2015-10-06 Fixed problems
    - Begun testing the secondary tactic
    - Minor recalibration. Still iffy on Colour and Sonar.
    - Added IR camera example code
    [IRPosition.ino, config.h, sensor_core.cpp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]
2015-10-06 Many bug fixes to secondary tactic. Still has work to do
    [config.h, sensor_core.cpp, sensor_core.h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]
2015-10-08 Restructure of movement algorthm
    It's now based on all three sensors. Still has a way to go...
2015-10-09 just in case...
2015-10-10 IMU may be working
2015-10-10 Got DIP switch working
    Switches 2, 6 and 8 don't work
2015-10-10 Hackily fixed colour sensor (will have to recalibrate on day)
    [config.h, tactics_core.cpp]
2015-10-10 Attempted to fix 'stuck' condition.
    Still doesn't work!! >:(
    [config.h, sensor_core.cpp, sensor_core.h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]
2015-10-10 Minor change to getting stuck detection
    Even though it doesn't always figure out when it's stuck, hopefully this
    change will actually make it reverse!
    [tactics_core.cpp]
2015-10-11 Few modifications, stuck code?
    [tactics_core.cpp]
2015-10-11 More fixes, including for base behaviour and steppers
    [config.h, tactics_core.cpp]
2015-10-11 extending magnets works, auto base detect then retract magnets
2015-10-11 fixed weird base no target
    [tactics_core.cpp]
2015-10-11 magnets retracting good now
